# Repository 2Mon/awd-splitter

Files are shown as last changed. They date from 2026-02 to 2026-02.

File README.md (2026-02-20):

# awd-splitter
105c rated AWD splitter pcb for 3d printers

I needed a simpler way to wire up AWD printers, so I decided to make a simple AWD splitter PCB. instead of running 12 sets of wires, 4 for motors and 8 for fans and thermistors, this means you only need to run two big 16 channel wires down to your electronics bay. On the other end of the big wires, you can just use another one of these PCBs to break it back out and connect it to your mainboard, or just crimp individual connectors on the other end. This supports four motors for AWD, as well as a thermistor and cooling fan for each. It is rated to 105c chamber temps (limited by the connectors) but could likely go higher if needed. 

To use this project, solder the connectors onto the top side of the board. Crimp your motor wires and plug them into the motor ports. Take a 16 pin connector and wire it down to your electronics bay. Do the same for the thermistors and fans if desired. 

Screenshot 2026-02-19 at 7 44 39 PM

The PCB itself is very simple, but I tried to keep it fairly compact so it can fit easily anywhere on a printer. It uses Molex Nanofit connectors for high temp resistance and ease of crimping. 

Screenshot 2026-02-19 at 7 45 32 PM

^^ wiring info also printed on PCB!

| Item | Price ($) | Quantity | Total ($) | Link |
|---|---|---|---|---|
| Nanofit 2x8 | 4.60 | 4 | 18.40 | https://www.digikey.com/en/products/detail/molex/1053101216/6164149? |
| Nanofit 1x4 | 1.11 | 8 | 8.88 | https://www.digikey.com/en/products/detail/molex/1053091204/6131609? |
| Nanofit 1x2 | 0.95 | 16 | 15.20 | https://www.digikey.com/en/products/detail/molex/1053091202/6131607? |
| Nanofit 2x8 connector | 0.98 | 4 | 3.92 | https://www.digikey.com/en/products/detail/molex/1053081216/6164114? |
| Nanofit 1x4 connector | 0.41 | 8 | 3.28 | https://www.digikey.com/en/products/detail/molex/1053071204/6131602? |
| Nanofit 1x2 connector | 0.35 | 16 | 5.60 | https://www.digikey.com/en/products/detail/molex/1053071202/6131600? |
| Crimp | 0.11 | 140 | 15.4 | https://www.digikey.com/en/products/detail/molex/1053002100/7693143? |
| PCB | 3.60 | 1 | 3.60 | JLCPCB |

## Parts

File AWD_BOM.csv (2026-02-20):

item | price | quantity | total | link
Nanofit 2x8 | 4.6 | 4 | 18.4 | https://www.digikey.com/en/products/detail/molex/1053101216/6164149
Nanofit 1x4 | 1.11 | 8 | 8.88 | https://www.digikey.com/en/products/detail/molex/1053091204/6131609?
Nanofit 1x2 | 0.95 | 16 | 15.2 | https://www.digikey.com/en/products/detail/molex/1053091202/6131607?s=N4IgTCBcDaIIwAYCsBmBBOOYEQLoF8g
Nanofit 2x8 connector | 0.98 | 4 | 3.92 | https://www.digikey.com/en/products/detail/molex/1053081216/6164114?s=N4IgTCBcDaIIwAYCsBmBAOAtHMcBsIAugL5A
Nanofit 1x4 connector | 0.41 | 8 | 3.28 | https://www.digikey.com/en/products/detail/molex/1053071204/6131602?s=N4IgTCBcDaIIwAYCsBmBB2QiARzAgLCALoC%2BQA
Nanofit 1x2 connector | 0.35 | 16 | 5.6 | https://www.digikey.com/en/products/detail/molex/1053071202/6131600?s=N4IgTCBcDaIIwAYCsBmBB2QiARzAiBdAXyA
crimp | 0.11 | 140 | 15.4 | https://www.digikey.com/en/products/detail/molex/1053002100/7693143?s=N4IgTCBcDaIAQEYAMBWAzEphEAjMpIBdAXyA
 |  |  | 0
PCB | 3.60 | 1 | 3.60
 |  |  | 0
 |  |  | 0
 |  |  | GRAND TOTAL
 |  |  | 74.28

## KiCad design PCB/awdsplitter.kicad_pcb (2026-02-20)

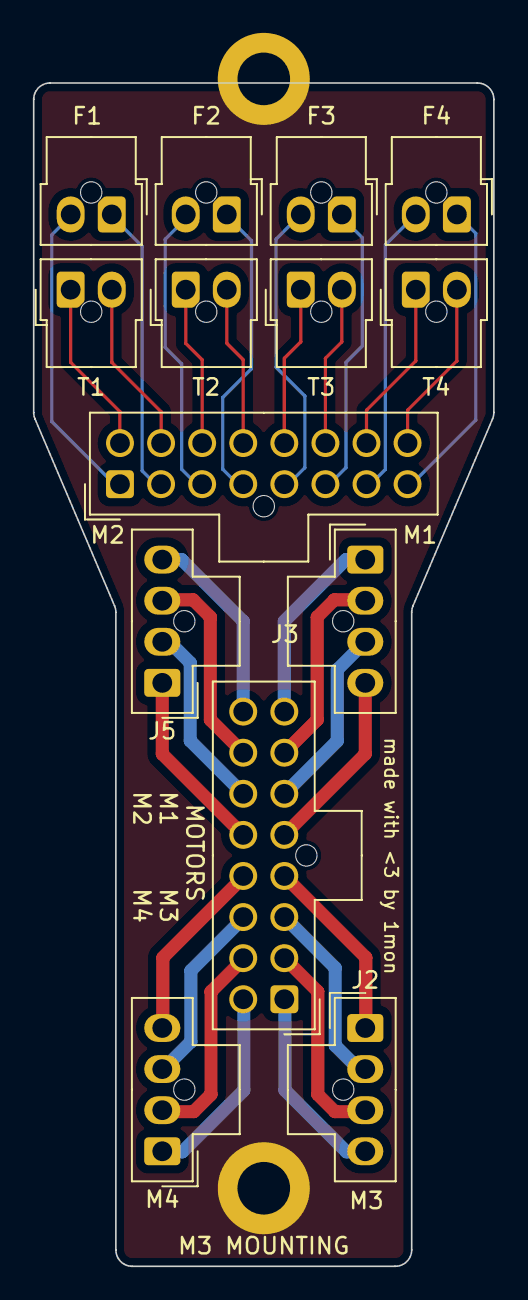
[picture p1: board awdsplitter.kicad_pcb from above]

Board: 2 copper layers, 28.0 x 72.0 mm, 16 parts (0 on the bottom side), 33 nets.

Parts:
F1, F2, F3, F4: MICROFIT_1x2_THT_V; Molex_Nano-Fit_105309-xx02_1x02_P2.50mm_Vertical
J1, J8: MICROFIT_2x8_THT_V; Molex_Nano-Fit_105310-xx16_2x08_P2.50mm_Vertical
J2, J5: MICROFIT_1x4_THT_V; Molex_Nano-Fit_105309-xx04_1x04_P2.50mm_Vertical
M1, M4: MICROFIT_1x4_THT_V; Molex_Nano-Fit_105309-xx04_1x04_P2.50mm_Vertical
M3 MOUNTING, M3 MOUNTING#2: MountingHole_Pad; MountingHole_3.2mm_M3_DIN965_Pad
T1, T2, T3, T4: MICROFIT_1x2_THT_V; Molex_Nano-Fit_105309-xx02_1x02_P2.50mm_Vertical

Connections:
/F1 +: F2.2, J8.3
/F1 -: F2.1, J8.4
/F2 +: F4.2, J8.7
/F2 -: F4.1, J8.8
/F3 +: J8.11, T2.1
/F3 -: J8.12, T2.2
/F4 +: J8.15, T4.1
/F4 -: J8.16, T4.2
/M1 A+: J1.1, J2.4
/M1 A-: J1.2, J2.3
/M1 B+: J1.3, J2.2
/M1 B-: J1.4, J2.1
/M2 A+: J1.5, M1.4
/M2 A-: J1.6, M1.3
/M2 B+: J1.7, M1.2
/M2 B-: J1.8, M1.1
/M3 A+: J1.9, M4.1
/M3 A-: J1.10, M4.2
/M3 B+: J1.11, M4.3
/M3 B-: J1.12, M4.4
/M4 A+: J1.13, J5.1
/M4 A-: J1.14, J5.2
/M4 B+: J1.15, J5.3
/M4 B-: J1.16, J5.4
/T1 A: F1.2, J8.1
/T1 B: F1.1, J8.2
/T2 A: F3.2, J8.5
/T2 B: F3.1, J8.6
/T3 A: J8.9, T1.1
/T3 B: J8.10, T1.2
/T4 A: J8.13, T3.1
/T4 B: J8.14, T3.2
GND: M3 MOUNTING.1, M3 MOUNTING#2.1

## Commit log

2026-02-20 Create PCB
2026-02-20 add bom
2026-02-20 Update AWD_BOM.csv with new item entries
    [AWD_BOM.csv]
2026-02-20 Update Crimp connector pricing and link
2026-02-20 Update PCB price and quantity in README
    Updated PCB price and quantity in the connector table.
2026-02-20 Modify item prices and quantities in AWD_BOM.csv
    Updated prices and quantities for items in the BOM.
    [AWD_BOM.csv]
